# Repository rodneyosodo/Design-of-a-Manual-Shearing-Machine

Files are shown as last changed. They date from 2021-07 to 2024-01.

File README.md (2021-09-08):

# Design of a Manual Shearing Machine - Manufacturing-Technology-1-Project







## This project is done by:

1. Kelvin Gitu ENM221-0058/2017
2. Rodney David ENM221-0091/2017

## Manual Shearing Machine

Shearing is a method for cutting materials into small pieces using a shear knife using some force. Metal plates and sheets are cut using this method. The most predominant type of shearing machine is the hydraulic shearing machine. However, most small businesses are not able to acquire such machines and thus form our purpose. Our design is a simple manual shearing machine that can be readily made in a well-equipped workshop. It is also cheap to produce and can be done in a very short time. 
A computer-aided drawing of the machine is shown below.

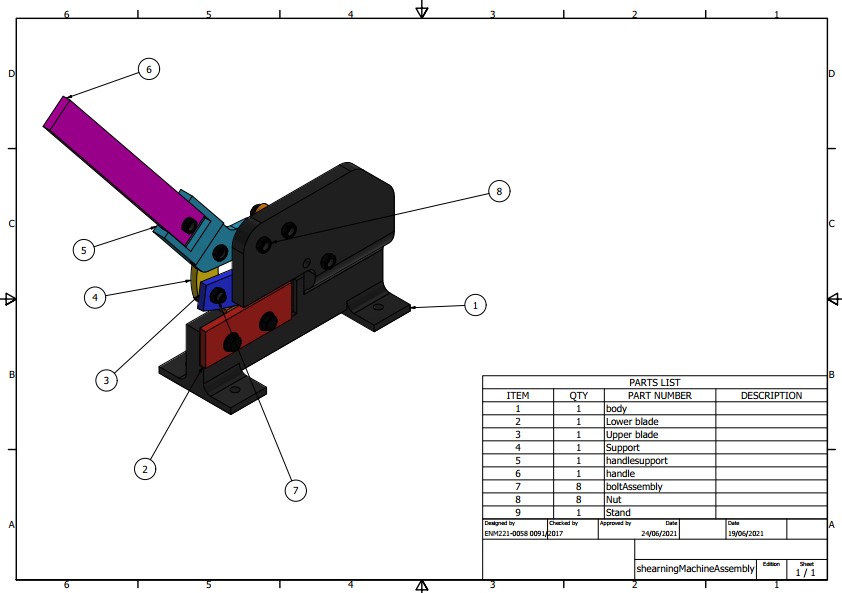
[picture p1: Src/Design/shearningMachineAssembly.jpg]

The assembly above consists of nine parts all of which can be produced in a workshop through processes such as turning, milling, shaping, drilling, among others. We also intend to use some of the parts from the shelves e.g bolt washer and nut. The handle might come as a rod or a tube with a rectangular cross-section from the manufacturer. This means it would have undergone some primary shaping. We would only need to surface finish it by grinding off unwanted material and painting.

## Manufacturing Processes

Primary shaping. As we had stated early some parts will come directly from the manufacturer. This includes the handle we can use a cylindrical handle or a cuboid handle. Probably it would have undergone a drawing operation.
Separation
1. Milling. This will be one of our core manufacturing processes. We can mill the remaining parts but we would prefer to use a CNC milling machine so as to achieve a high level of precision. We might use milling operations to the nut and bolt if they can not be found locally.
2. Lathe operations. The bolt washer and nut if they are not found locally we would start them off with lathe operations. These would include facing, turning, drilling, threading among others,
3. CNC Machining. Now, all the above operations can be completed in a programmable CNC machine. I guess this is our most important process. We wouldn’t discuss the advantages of CNC machining presents to use but we would rather explain some of the machining processes. We would use CNC milling to do most of our tasks. We would initially buy the billet material then place it on the milling table and program the machine to cut the specific geometry we want. Some of the parts we would mill include the Body, lower blade, upper blade, support, handle support and stand. 
4. Grinding. After machining the upper and lower blade we would grind it so as to ensure the knife edge is sharp enough. We aren’t sure if this can be done using the MasterCAM software but we are looking into it.
Joining
1. Welding. We intend to reinforce some of the bolted joints with welds specifically at the body. This is to ensure our body is rigid and has a longer life span. We aren’t sure if this can be done using the MasterCAM software but we are looking into it. We know it can be done using the Inventor CAM software.
2. Bolt and nut. This is the easiest and most convenient way to join some of our parts e.g the handle and also the blades to the body. This would provide a good joint ensuring the machining can last longer.
Coating
As our final process, we would like to paint the machine so as to increase its aesthetic appeal. We aren’t sure if this can be done using the MasterCAM software but we are looking into it.

## Presentation
Can be viewed from [here](https://prezi.com/view/DIa9HizP2NmdG6Iu90mM/)

## Project structure
```
.
├── Analysis
│   ├── 2021-07-30_22-48-34.mkv
│   ├── Images
│   │   ├── Autodesk_Logo_Black.png
│   │   ├── minus.png
│   │   ├── plus.png
│   │   └── shearningMachineAssembly.iam Stress Analysis Report 30_07_2021
│   │       └── 0
│   │           ├── Constraint_0_0.png
│   │           ├── Load_0_1.png
│   │           ├── Load_0_2.png
│   │           ├── Result_1_1.png
│   │           └── Result_1_8.png
│   ├── shearningMachineAssembly.iam Stress Analysis Report 30_07_2021.html
│   ├── Study Result.avi
│   └── Weld Bead Report.xls
├── Codes
│   ├── 1001.nc
│   ├── bodybottompart.mpf
│   ├── bodybottompart.NC
│   ├── upperblade.mpf
│   └── upperblade.NC
├── Design
│   ├── handle.dwg
│   ├── handle.ipt
│   ├── handle.pdf
│   ├── handlesupport.dwg
│   ├── handlesupport.ipt
│   ├── handlesupport.pdf
│   ├── lockfile.lck
│   ├── OldVersions
│   ├── README.md
│   ├── rendershearningMachineAssembly.png
│   ├── shearningMachineAssembly
│   │   ├── AIP
│   │   │   └── FEA
│   │   │       ├── dola00nj4.fins
│   │   │       └── Simulation.log
│   │   └── InCAD
│   │       └── FEA
│   │           ├── LICENSE.LOG
│   │           ├── pkfd50uhz.ECD
│   │           └── pkfd50uhz.OUT
│   ├── shearningMachineAssembly.dwg
│   ├── shearningMachineAssembly.iam
│   ├── shearningMachineAssembly.jpg
│   └── shearningMachineAssembly.pdf
├── MANUAL_SHEARING_MACHINE_PROJECT_REPORT.pdf
├── presentation.txt
└── README.md
```

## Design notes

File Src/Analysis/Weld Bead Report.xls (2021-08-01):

Document | ID | Type | Length | UoM | Mass | UoM | Area | UoM | Volume | UoM
C:\Users\Public\D\Desktop\Trash\Manufacturing-Technology-1-Project\Src\Design\bodyAssembly.iam
 | Fillet Weld 1 | Fillet | 110 | mm | 0.023 | kg | 5872.448 | mm^2 | 8443.037 | mm^3 | 110 mm | 0.023 kg | 5872.448 mm^2 | 8443.037 mm^3
 | Fillet Weld 2 | Fillet | 110 | mm | 0.023 | kg | 5872.448 | mm^2 | 8443.037 | mm^3 | 110 mm | 0.023 kg | 5872.448 mm^2 | 8443.037 mm^3
 | Fillet Weld 3 | Fillet | 50 | mm | 0.005 | kg | 1797.566 | mm^2 | 2026.715 | mm^3 | 50 mm | 0.005 kg | 1797.566 mm^2 | 2026.715 mm^3
 | Fillet Weld 4 | Fillet | 50 | mm | 0.005 | kg | 1797.566 | mm^2 | 2026.715 | mm^3 | 50 mm | 0.005 kg | 1797.566 mm^2 | 2026.715 mm^3
 | Fillet Weld 5 | Fillet | 50 | mm | 0.005 | kg | 1797.566 | mm^2 | 2026.715 | mm^3 | 50 mm | 0.005 kg | 1797.566 mm^2 | 2026.715 mm^3
 | Fillet Weld 6 | Fillet | 50 | mm | 0.005 | kg | 1797.566 | mm^2 | 2026.715 | mm^3 | 50 mm | 0.005 kg | 1797.566 mm^2 | 2026.715 mm^3
 |  |  | Length | Mass | Area | Volume
 | Fillet Weld 1 | Fillet | 110 mm | 0.023 kg | 5872.448 mm^2 | 8443.037 mm^3
 | Fillet Weld 2 | Fillet | 110 mm | 0.023 kg | 5872.448 mm^2 | 8443.037 mm^3
 | Fillet Weld 3 | Fillet | 50 mm | 0.005 kg | 1797.566 mm^2 | 2026.715 mm^3
 | Fillet Weld 4 | Fillet | 50 mm | 0.005 kg | 1797.566 mm^2 | 2026.715 mm^3
 | Fillet Weld 5 | Fillet | 50 mm | 0.005 kg | 1797.566 mm^2 | 2026.715 mm^3
 | Fillet Weld 6 | Fillet | 50 mm | 0.005 kg | 1797.566 mm^2 | 2026.715 mm^3

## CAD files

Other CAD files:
Src/Design/bodyAssembly.dwg
Src/Design/shearningMachineAssembly.dwg
Src/Design/Stand.dwg
Src/Design/handlesupport.dwg
Src/Design/handle.dwg
Src/Design/Upper blade.dwg
Src/Design/Support.dwg
Src/Design/Lower blade.dwg
Src/Design/body.dwg
Src/Design/OldVersions/shearningMachineAssembly.0003.dwg
Src/Design/OldVersions/bodyAssembly.0002.dwg
Src/Design/OldVersions/Stand.0002.dwg
Src/Design/OldVersions/Lower blade.0001.dwg
Src/Design/OldVersions/Support.0001.dwg
Src/Design/OldVersions/body.0001.dwg
Src/Design/Bolt.ipt
Src/Design/Lower blade.ipt
Src/Design/Nut.ipt
Src/Design/OldVersions/Bolt.0005.ipt
Src/Design/OldVersions/Lower blade.0005.ipt
Src/Design/OldVersions/Nut.0002.ipt
Src/Design/OldVersions/Stand.0004.ipt
Src/Design/OldVersions/Support.0004.ipt
Src/Design/OldVersions/Support.0005.ipt
Src/Design/OldVersions/Upper blade.0009.ipt
Src/Design/OldVersions/Washer.0004.ipt
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

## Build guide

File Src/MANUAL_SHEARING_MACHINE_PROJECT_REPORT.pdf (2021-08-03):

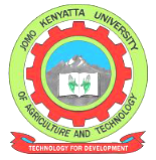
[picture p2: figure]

### JOMO KENYATTA UNIVERSITY OF AGRICULTURE AND TECHNOLOGY

### COLLEGE: COLLEGE OF ENGINEERING AND TECHNOLOGY

### SCHOOL: SCHOOL OF MATERIAL, MECHANICAL AND MANUFACTURING ENGINEERING

### DEPARTMENT: DEPARTMENT OF MECHATRONICS ENGINEERING

### UNIT CODE: EMT 2440

### UNIT TITLE: MANUFACTURING TECHNOLOGY

### YEAR OF STUDY: 4

TH

### ACADEMIC YEAR: 2021

### TASK: MANUAL SHEARING MACHINE PROJECT

NAME | REGISTRATION NO
KELVIN GITU | ENM221-0058/2017
RODNEY OSODO | ENM221-0091/2017

## Table of Contents

Abstract | 2
Introduction | 2
Problem Definition | 3
Design Requirements | 3
Design Description | 4
Design and Manufacturing Process | 5
Machining | 5
Body | 6
Lower blade | 8
Upper blade | 8
Stand | 9
Support | 10
Handle support | 11
Washer | 12
Joining | 12
Coating | 12
Evaluation | 13
Conclusion | 15
Challenges | 15
References | 16
Appendix | 17

## Abstract

This report presents the design of a manual shearing machine which is designed to increase the thickness of material it can cut in such a manner that the shearing force is great enough to cut material of width greater than 20mm. The objective of this project was to come up with a shearing machine that improves productivity by reducing labour costs (easy to use), meets client needs for small businesses by providing a design that can be fabricated in a workshop and increases worker safety. This is done by modifying the existing shearing machine by increasing blade angles and also increasing the structural rigidity of the shearing machine. The parts are modelled in Autodesk Inventor and machined using the Inventor CAM plugin. We made considerations in dimension and materials used so that the assembly could be manufactured locally at the machine shop.

## Introduction

A shearing machine is a machine that cuts a sheet of metal by reciprocating a linear motion with one blade moving relative to a fixed blade. Shearing is a general name for most sheet metal cutting, but in a specific sense, designates a cut in a straight line across a strip, sheet or bar. This procedure leaves a clean edge on the piece of the metal that is sheared or cut. Shearing machines are used to cut or shear metal sheets in many ways. The particular method chosen depends on several factors such as the size and shape of the parts required and the numbers needed. The moving cutting member of a shearing machine may be actuated by a hand lever in bench shearing machines, foot treadle in treadle guillotines or electric motor or hydraulic system in power guillotines.

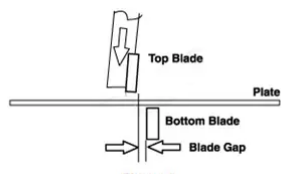
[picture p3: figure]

Figure 1: How shearing is done

## Problem Definition

During our attachment at the welding shop, we were able to encounter the manual shearing machine. Currently, it is able to cut up to a maximum of 20mm. This seems large but we saw an opportunity. We set out to increase the thickness the manual shearing machine could cut up to 30mm. Also, the shearing machines in the market include hydraulic swing beam shear, hydraulic guillotine shear, and electric shear. These off the shelf designs are very expensive and only top manufacturing plants can afford them. To make shearing available for small businesses, our design introduces a simple manual shearing machine that can be fabricated in a workshop at a relatively low cost. Our design is an adaptive redesign of an already existing solution, which has become outdated. The design is as shown below:

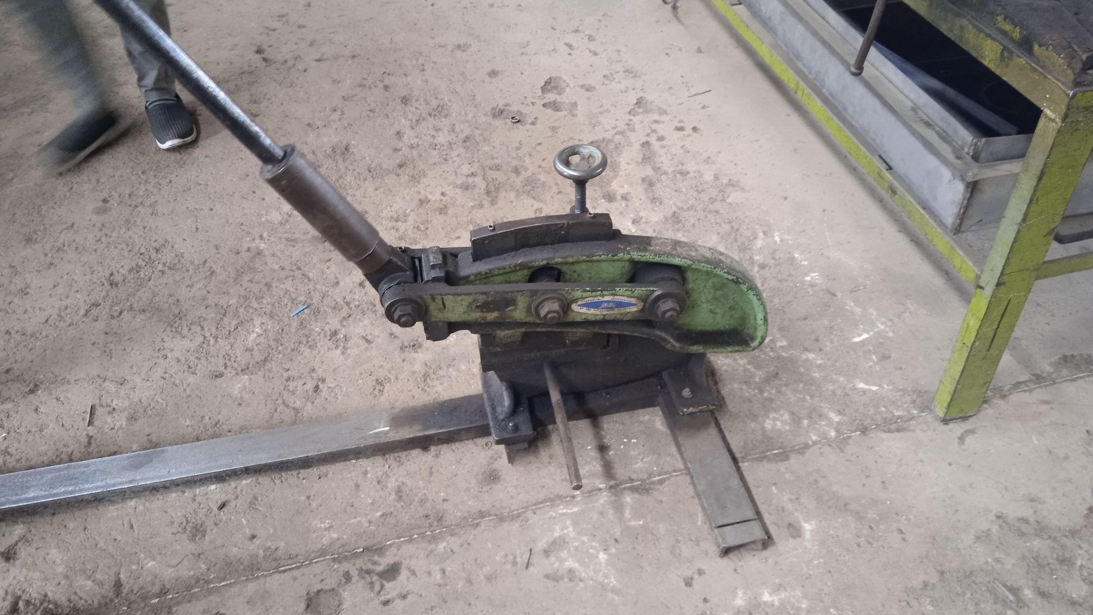
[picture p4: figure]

Figure 2: Manual Shearing Machine at Welding shop

## Design Requirements

The design shown in Figure 1 cuts sheet metal of up to 20mm. To improve on this design, we designed our manual shearing machine to shear sheets of up to 30mm.
The following formula is used to calculate the force required to shear sheet metal:

F = L • T • S
Where: F is the force required (Newtons), L is the length of the sheet to be cut (millimetres), T is the sheet thickness (millimetres) and S is the shear strength (N/mm ). ²

For a steel sheet metal with a thickness of 20mm, length is 20mm and shear strength of 300MPa, the force required to cut the shear metal will be:

F = L * T * S

F = 20 * 20 * 300

F = 120kN
Now, our design is supposed to do better, by generating enough force to cut up to 30mm thick of sheet metal.

F = 20 * 30 * 300

F = 180kN
This will be the requirement for our design. We also intend for our design to reduce labour costs, increase worker safety and increase the productivity of the process.

## Design Description

The design selected is constructed using only nine main parts from material that can be found readily: a combination of mild steel and stainless steel. The manual shearing machine has an upper and lower blade from which a sheet of metal can be cut. The upper blade is part of a lever system together with the handle through which shearing force is applied. The lower blade is fixed to the body part of the shearing machine which has a large surface area to absorb the pressure due to the shearing force and increase the stability of the machine. During a shearing operation, a sheet of metal is placed on the lower fixed blade, and a cutting force is applied through the handle. When the two blades make contact, the sheet metal is broken and separated according to the desired dimensions. The design is as shown in Figure 3.

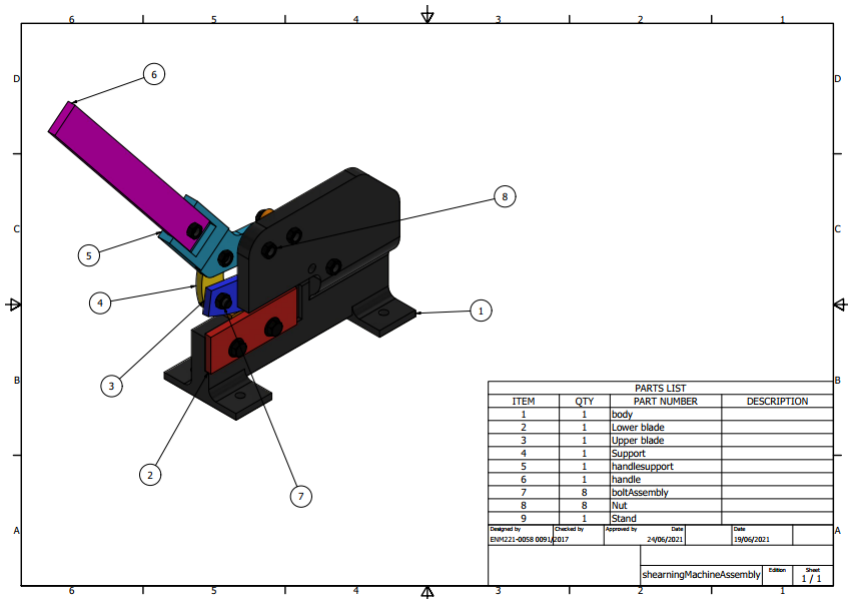
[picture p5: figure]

Figure 3. CAD Drawing of the Manual Shearing Machine

## Design and Manufacturing Process

The manual shearing machine design is an assembly of various parts and to describe its production process, we need to discuss the manufacture of the individual parts. In coming up with the parts, various workshop processes are applied, including turning, milling, drilling, among others. Some parts such as the fasteners (nuts and bolts), the washer and the handle were bought off the shelf. The other parts were first developed using CAD software, and we used Autodesk Inventor.
Manufacturing processes applied include:

### 1. Machining

CNC Machining. This is the most important machining process as most of our parts will be produced in a CNC machine. We will initially buy the billet material then place it on the milling table and program the machine to cut the specific geometry we want. Some of the parts we mill include the body, lower blade, upper blade, support, handle support and stand. The CNC milling process has four distinct stages:
- CAD model design.
- CAD model design conversion to a CNC program
- CNC milling machine setup
- Milling operation execution
Now let us take a look at the various parts, their CAD model designs, and their CNC programs to be executed in a milling machine. A computer-aided manufacturing software will be used to generate the CNC program. We decided to use the Siemens 840D due to its similarity with the CNC machine at the machine shop. This will actually help us do the physical analysis of our design if we were to be given a go-ahead to machine one of the parts.
a. Body

To produce the body in Figure 4, we decided to use a modular approach since machining the whole body altogether is a difficult operation. We broke the body into 3 main pieces, the bottom part, the top part and the standoffs. These individual parts are now able to be machined using a milling operation. We set up an initial stock which is an extra 5 mm at the top and an extra 2mm on the sides. The first operation was facing the required height of the workpiece. This was done with even multiple depths of 2mm spacing. Then we followed up by adaptive milling which is a 3D milling technique. We finally finished up with drilling the holes onto the workpiece. This operation was the same for all the parts of the body. We used flooding when applying coolant since our tool could not be able to deliver coolant inside. We thought of using air suction by keeping in mind the CNC at the machine shop, so we decided flooding was the better approach. We then used two joining techniques; welding and the use of nuts and bolts. We joined the standoffs to the bottom part with welding after having placed the bottom part in a slot on the standoffs. Joining the top part and bottom part was done mainly using the nuts and bolts. We finally reinforced it using welding with a fillet shape. The weld bead report is in Table 1.

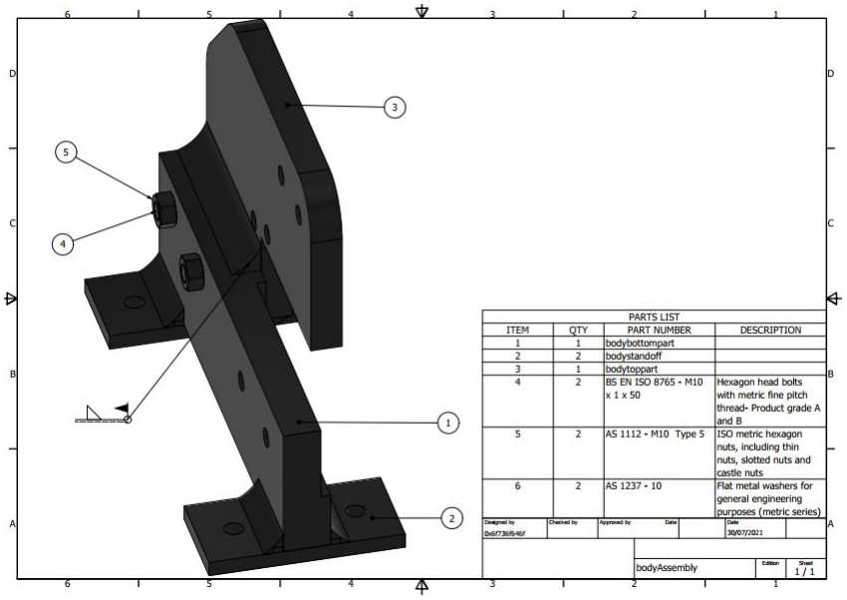
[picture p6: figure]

Figure 4. CAD Model of the Body

| | Length | Mass | Area | Volume
Fillet Weld 1 | Fillet | 110 mm | 0.023 kg | 5872.448 mm 2 | 3 8443.037 mm
Fillet Weld 2 | Fillet | 110 mm | 0.023 kg | 5872.448 mm 2 | 3 8443.037 mm
Fillet Weld 3 | Fillet | 50 mm | 0.005 kg | 1797.566 mm 2 | 3 2026.715 mm
Fillet Weld 4 | Fillet | 50 mm | 0.005 kg | 1797.566 mm 2 | 3 2026.715 mm
Fillet Weld 5 | Fillet | 50 mm | 0.005 kg | 1797.566 mm 2 | 3 2026.715 mm
Fillet Weld 6 | Fillet | 50 mm | 0.005 kg | 1797.566 mm 2 | 3 2026.715 mm

Table 1: Weld bead report

b. Lower blade

To come up with the lower blade the first manufacturing operation was facing, using a face mill of diameter 50mm. This operation reduced the workpiece to the required height. One edge was turned at an angle as it would form the cutting edge of the blade. Since we have a sloping cutting edge we decided to place it in a Z-direction such that the slant was an incremental downwards slope. We used additive machining, a form of 3D machining, to be able to obtain the contours on the blade. Once the dimensions of the part were achieved, the two 10 mm diameter holes were created using a drill using the rapid out technique.

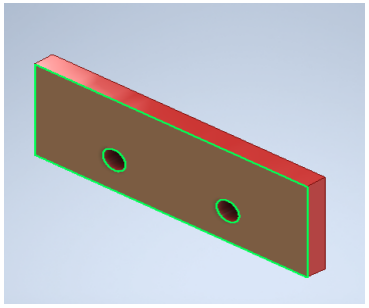
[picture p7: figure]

Figure 5. CAD Model of the Lower Blade

c. Upper blade

Face milling, end milling, and drilling are the operations carried out to come up with this part. We first reduced the workpiece to the required height using a face mill, which was followed by adaptive milling to establish the shape of the blade. In this operation, the milling tool axially follows the path with a predefined geometry. The two holes that would form the assembly were drilled into place.

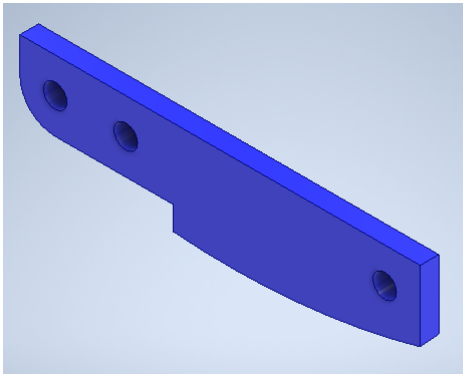
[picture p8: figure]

Figure 6. CAD Model of Upper Blade

d. Stand

Due to its design complexity, we decided to do a modular approach too. Here we split the stand into three different parts. The circular part was turning on a CNC lathe while the supporting beam together with the base was milled. For the circular part, we bought stock then we faced it off. This was done by a right-hand turning tool. We set the centre point at an offset of 1 mm from the true centre in order to get all of the material out during facing. We did multiple passes with 3 passes 2 mm apart. We continued to the turning where we defined it as profile roughing. We turned up to the end of the workpiece. We did multiple passes 1 mm apart. We then drilled the inside hole using the rapid out technique up to the end and finally parted off the workpiece from the stock using a grooving tool.

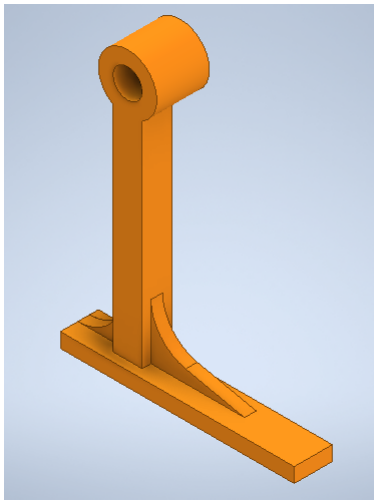
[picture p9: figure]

Figure 7. CAD Model of the Stand

e. Support

We first reduced the height of the workpiece using a facing operation. The two holes were drilled into place. We then machined the part using adaptive milling which maintains a consistent tool path and chip load which results in faster, smoother cutting.

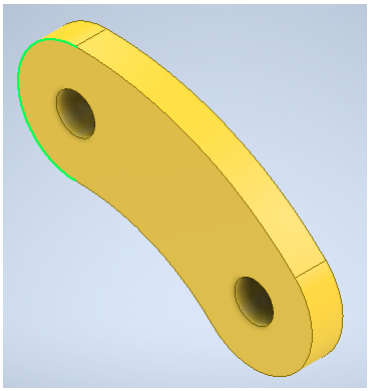
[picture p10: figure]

Figure 8. CAD Model of the Support

f. Handle support

We initially intended to use plasma cutting but the plasma cutting at the welding workshop isn’t CNC operated. We then decided to use the milling operation. Two facing operations were conducted to come up with the two heights on the other side of the top of the workpiece. On one end of the workpiece, we created a flat bottomed cavity using another end milling operation. Joining holes were drilled into the workpiece, after which the final operation, adaptive milling, was executed.

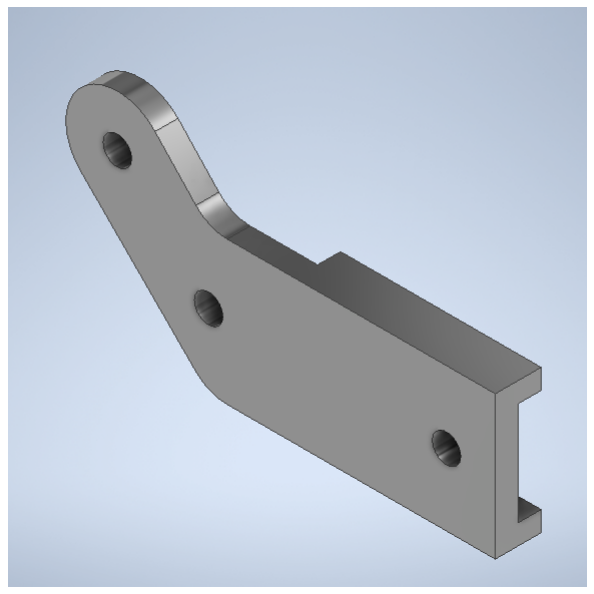
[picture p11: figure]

Figure 9. CAD Model of the Handle Support

g. Washer

This was purchased at the local stores together with the nuts and bolts used for assembly

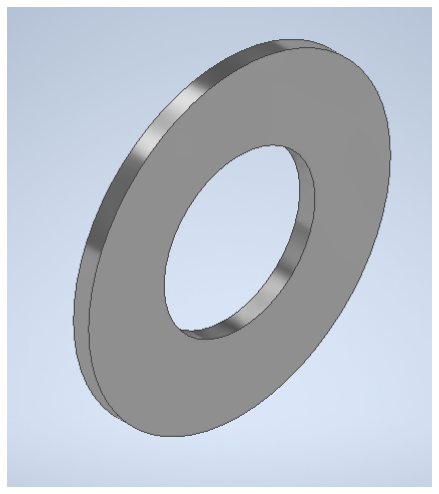
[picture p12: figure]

Figure 10. CAD Model of the Washer

### 2. Joining

After coming up with the individual parts, we need to put multiple parts together to make one piece. Some of the joining processes used include welding and the use of fasteners (nuts and bolts). The body is fabricated as three parts and joined together using a weld. Arc welding is the most preferred method.

The other parts are assembled together using the fasteners. The lower blade is attached to the body using bolts and nuts. The support, handle, handle support and upper blade are all joined together using bolts and nuts.

### 3. Coating

The final manufacturing process is coating both for aesthetic value and to protect against surface corrosion, that is, rusting.

## Evaluation

After coming up with the design, and manufacturing of the shearing machine, we need to make sure it works by simulating it in the CAD software.
This was done through dynamic simulation and Finite element analysis. For Dynamic simulation, we introduced a torque of 300.000 N/mm on the pivot of the lower blade to be able to see if the handle could be driven down to simulate the pressing action. This was justified as the handle moved down simulating the cutting mechanism. We also checked our mechanism and found out that 4 bodies were mobile with a 1 degree of freedom.
For the Finite Element Analysis, we were testing the maximum load the shearing machine can hold before fracture. We placed a test material on the bed which produces an opposite force of magnitude 10N majorly on the z-axis. We then added a 100N push force on the handle and observed the changes. The body was selected to be fixed while the blade had a frictionless surface to allow smooth motion.
Name | Steel, Mild
General | Mass Density | 7.85 g/cm^3
| Yield Strength | 207 MPa
| Ultimate Tensile Strength | 345 MPa
Stress | Young's Modulus | 220 GPa
| Poisson's Ratio | 0.275 ul
| Shear Modulus | 86.2745 GPa
Part Name(s) | Body.ipt, Lower blade.ipt, Upper blade.ipt, Support.ipt, handlesupport.ipt, handle.ipt, Stand.ipt

Name | Stainless Steel
General | Mass Density | 8 g/cm^3
| Yield Strength | 250 MPa
| Ultimate Tensile Strength | 540 MPa
Stress | Young's Modulus | 193 GPa
| Poisson's Ratio | 0.3 ul
| Shear Modulus | 74.2308 GPa
Part Name(s) | Bolt.ipt, Washer.ipt, Nut.ipt, Bolt.ipt

Table 2: Initial conditions

From our results, we were able to see that this motion induced a reaction moment of 1.12543 Nm.

Name | Minimum | Maximum
Volume | 1112060 mm^3
Mass | 8.73379 kg
Von Mises Stress | 0.000000946634 MPa | 5.50151 MPa
1st Principal Stress | -0.770633 MPa | 2.74524 MPa
3rd Principal Stress | -5.69371 MPa | 0.262106 MPa
Displacement | 0 mm | 0.00527388 mm
Safety Factor | 15 ul | 15 ul
Table 3: Finite Element Analysis

With a 15ul safety factor, we are at liberty to say that this machine increases its lifetime by a great margin. The maximum stress occurs at the cutting region demonstrated by Figure 10 below.

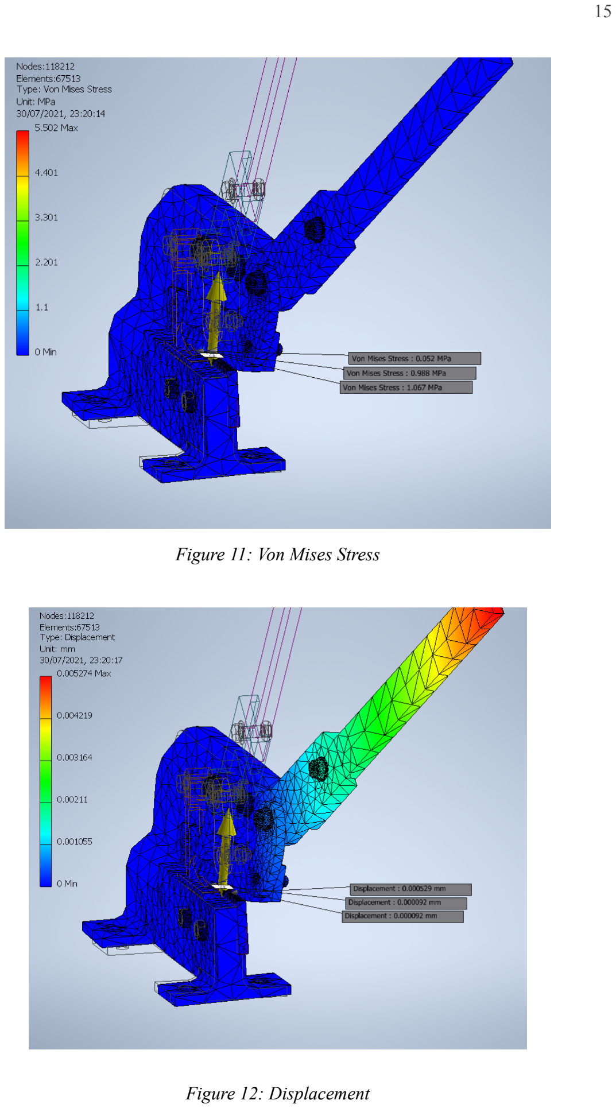
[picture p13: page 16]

Figure 11: Von Mises Stress

Figure 12: Displacement

As demonstrated we can be able to see that the handle is the one that moves, objecting to the physics behind the shearing machine.

## Conclusion

The design above seeks to employ a cheap and reliable way to cut sheets of metal. As the design procedure shows, it can be produced readily and quickly using basic workshop processes, including facing, turning, drilling among others. We have also proved that it has increased functionality compared to the previous design. As per our design requirements, our design increases the cutting force, thus enabling thicker sheets to be cut. Our design is also quite reliable as evidenced by the 15ul safety factor.

## Challenges

1. A complex design that needs casting processes.
2. Obtaining MasterCAM as it failed to start even with the Home education license.

## References

1. Merril L. Ridgeway, Kenneth E. Olding "MechanicalPress, Especially A Cupping Press", United StatesPatent, 3902347, (1975) Page 23 -30.
2. E. Paul. Degarmo, “Shearing in Metal Cutting”, Pages 518-528, Materials and Processes in Manufacturing, Eighth Edition, 2003, Prentice Hall of India Pvt Ltd.
3. Emil Gustafsson, “Experiments on sheet metal shearing”, Division of Mechanics of Solid Materials Department of Engineering Sciences and Mathematics Luleå University of Technology, SE-971 87 Luleå, Sweden
4. Z. Klim, E. Ennajimi, M. Balazinski and C. Fortin, Cutting Tool Reliability Analysis for Variable Feed Milling Of 17-4ph Stainless Steel.
5. Qehaja, N.; Bunjaku, A.; Salihu A. &Zeqiri, H., The Reliability of The Metal Cutting Tools on The Bases Of The Technological Criteria of Consumption Method
6. R. Hambli, A. Potiron, and A. Kobi, “Application Of Design Of Experiment Technique For Metal Blanking Processes Optimization,” Mécanique& Industries, vol. 4, no. 3, pp. 175
7. Joseph E. Shigley, Mechanical Engineering Design, Sixth Edition, Tata Mcgraw Hill, 2005.
8. Bhandari V.B., Design Of Machine Elements, eighteenth edition, Mcgraw Hill Companies, 2003.

## Appendix

1. https://github.com/KelvinGitu/Manufacturing-Technology-1-Project Project link
2. https://github.com/KelvinGitu/Manufacturing-Technology-1-Project/tree/main/Src/Co des (https://github.com/KelvinGitu/Manufacturing-Technology-1-Project/tree/main/Src/Codes) Machining codes
3. Example of milling part

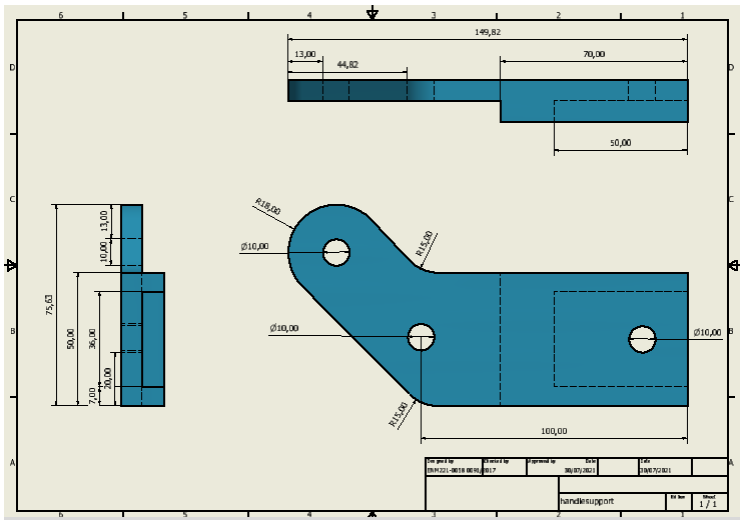
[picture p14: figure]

Figure 12: Handle support
4. Sample Generated codes for the handle support

; %_N_HANDLESUPPORT_MPF
N10 ; handlesupport
N11 ; T1 D=50 CR=0 - ZMIN=16 - face mill
N12 ; T2 D=5 CR=0 - ZMIN=0.51 - flat end mill
N13 ; T30 D=10 CR=0 TAPER=118deg - ZMIN=0 - drill
N14 WORKPIECE(,,,"BOX",112,21,0,80,74.91,37.815,-74.91,-37.815) N15 G90 G94
N16 G71
N17 G64
N18 G17
N19 G0 SUPA Z0 D0

N20 ; Face1
N21 T1 D1
N22 M6
N23 T2
N24 S955 M3
N25 G54
N26 G0 X107.41 Y-24.375
N27 G0 Z36
N28 M8
N29 G0 Z26

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
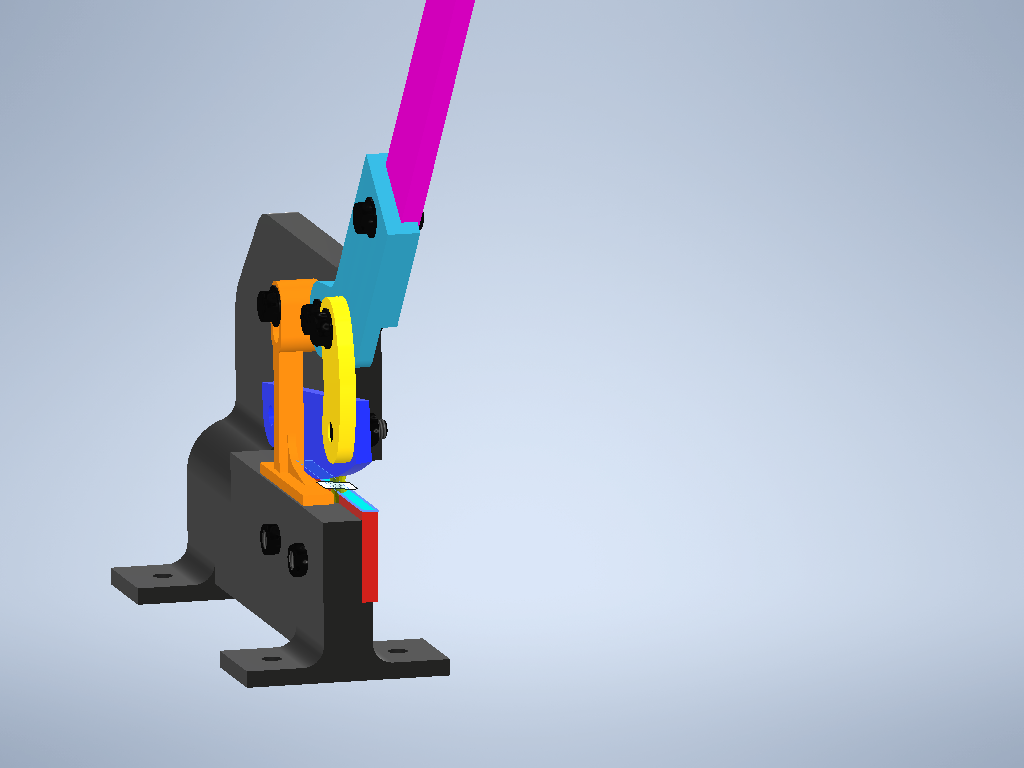
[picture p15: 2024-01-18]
Src/Analysis/Images/shearningMachineAssembly.iam Stress Analysis Report 30_07_2021/0/Load_0_1.png

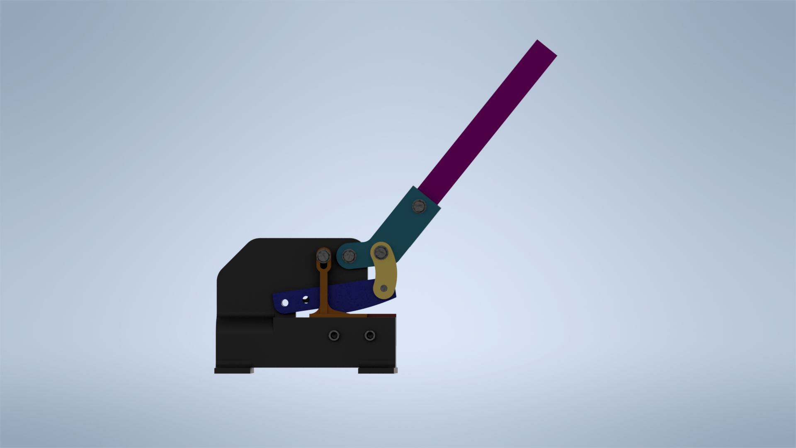
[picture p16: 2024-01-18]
Src/Design/rendershearningMachineAssembly.png

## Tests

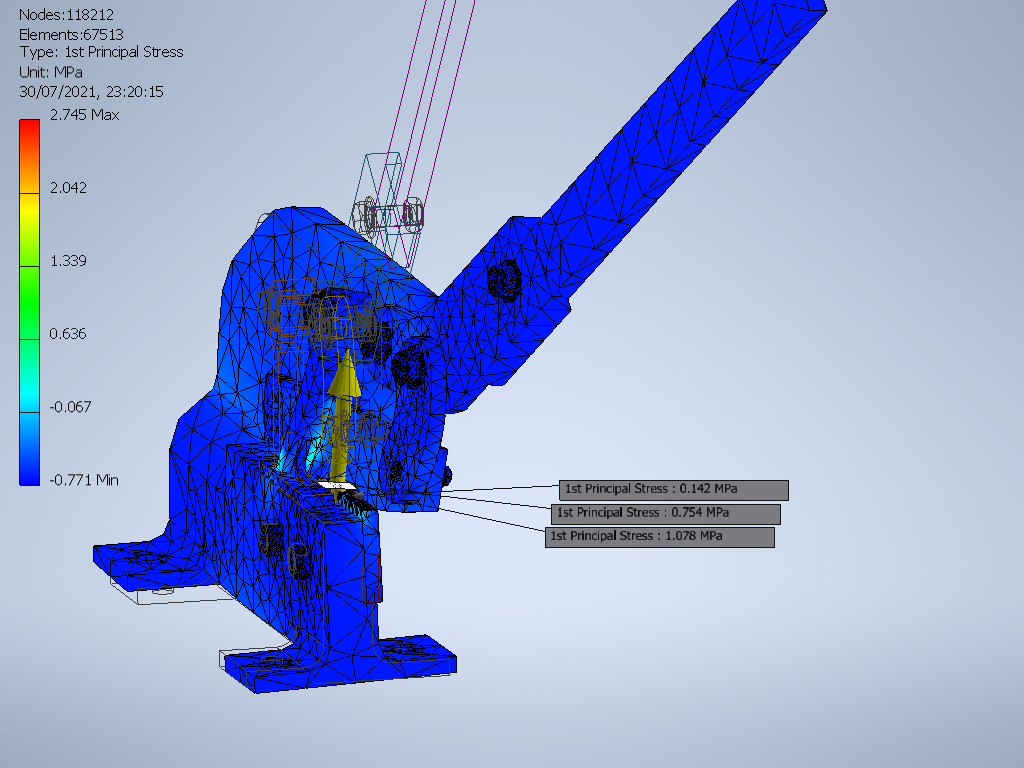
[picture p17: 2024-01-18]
Src/Analysis/Images/shearningMachineAssembly.iam Stress Analysis Report 30_07_2021/0/Result_1_6.png

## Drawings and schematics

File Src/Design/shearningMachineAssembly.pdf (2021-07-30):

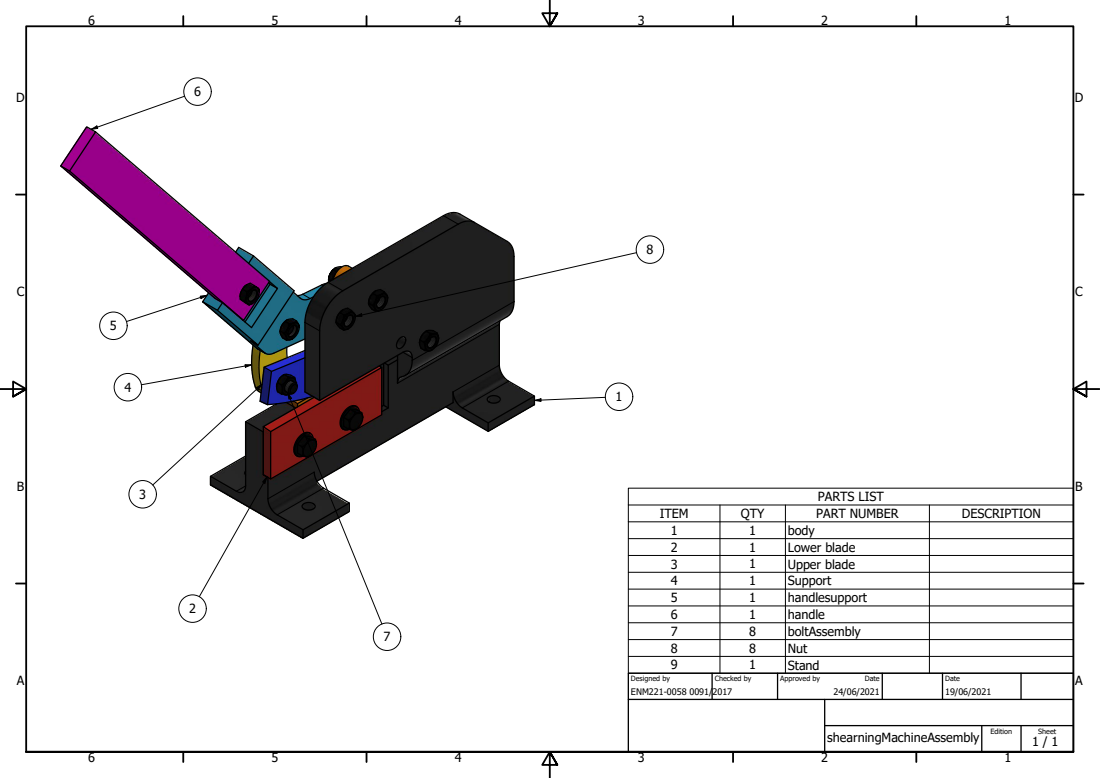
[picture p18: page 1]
PARTS LIST

ITEM | QTY | PART NUMBER | DESCRIPTION
1 | 1 | body
2 | 1 | Lower blade
3 | 1 | Upper blade
4 | 1 | Support
5 | 1 | handlesupport
6 | 1 | handle
7 | 8 | boltAssembly
8 | 8 | Nut
9 | 1 | Stand

Designed by ENM221-0058 0091/2017 | Checked by | Approved by Date 24/06/2021 | | Date 19/06/2021

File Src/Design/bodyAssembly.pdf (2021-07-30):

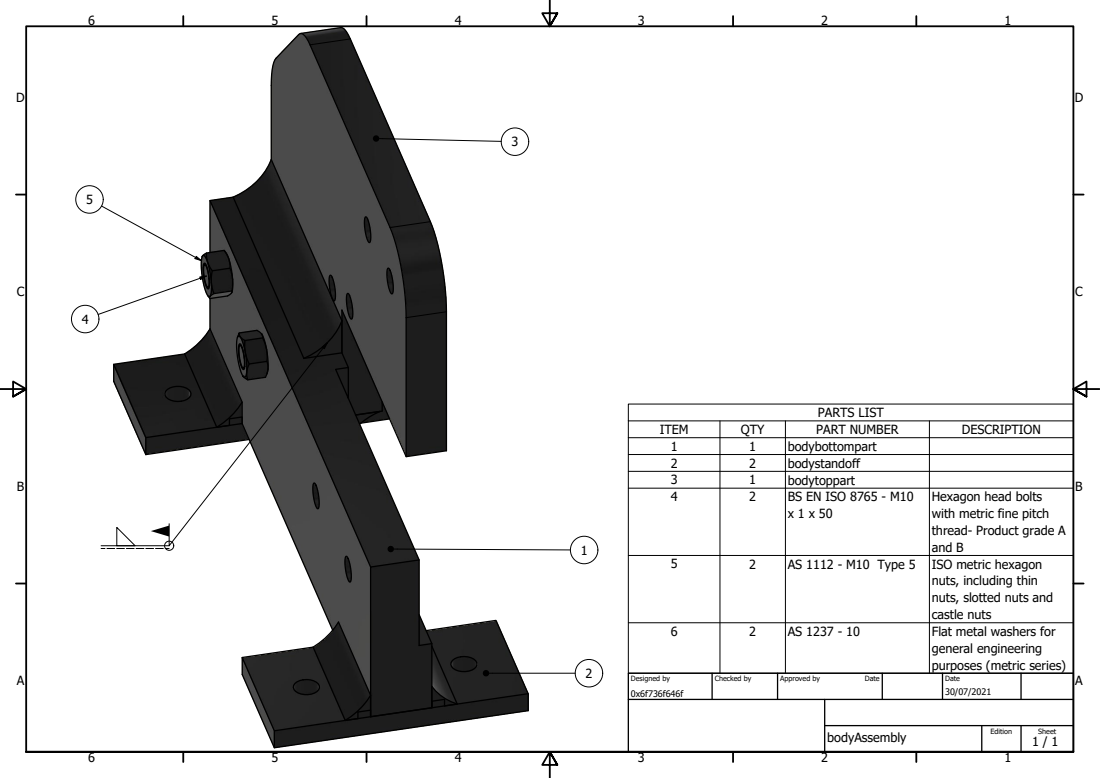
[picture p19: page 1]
PARTS LIST

ITEM | QTY | PART NUMBER | DESCRIPTION
1 | 1 | bodybottompart
2 | 2 | bodystandoff
3 | 1 | bodytoppart
4 | 2 | BS EN ISO 8765 - M10 x 1 x 50 | Hexagon head bolts with metric fine pitch thread- Product grade A and B

5 | 2 | AS 1112 - M10 Type 5 | ISO metric hexagon nuts, including thin nuts, slotted nuts and castle nuts

6 | 2 | AS 1237 - 10 | Flat metal washers for general engineering purposes (metric series)

Designed by 0x6f736f646f | Checked by | Approved by | | Date 30/07/2021

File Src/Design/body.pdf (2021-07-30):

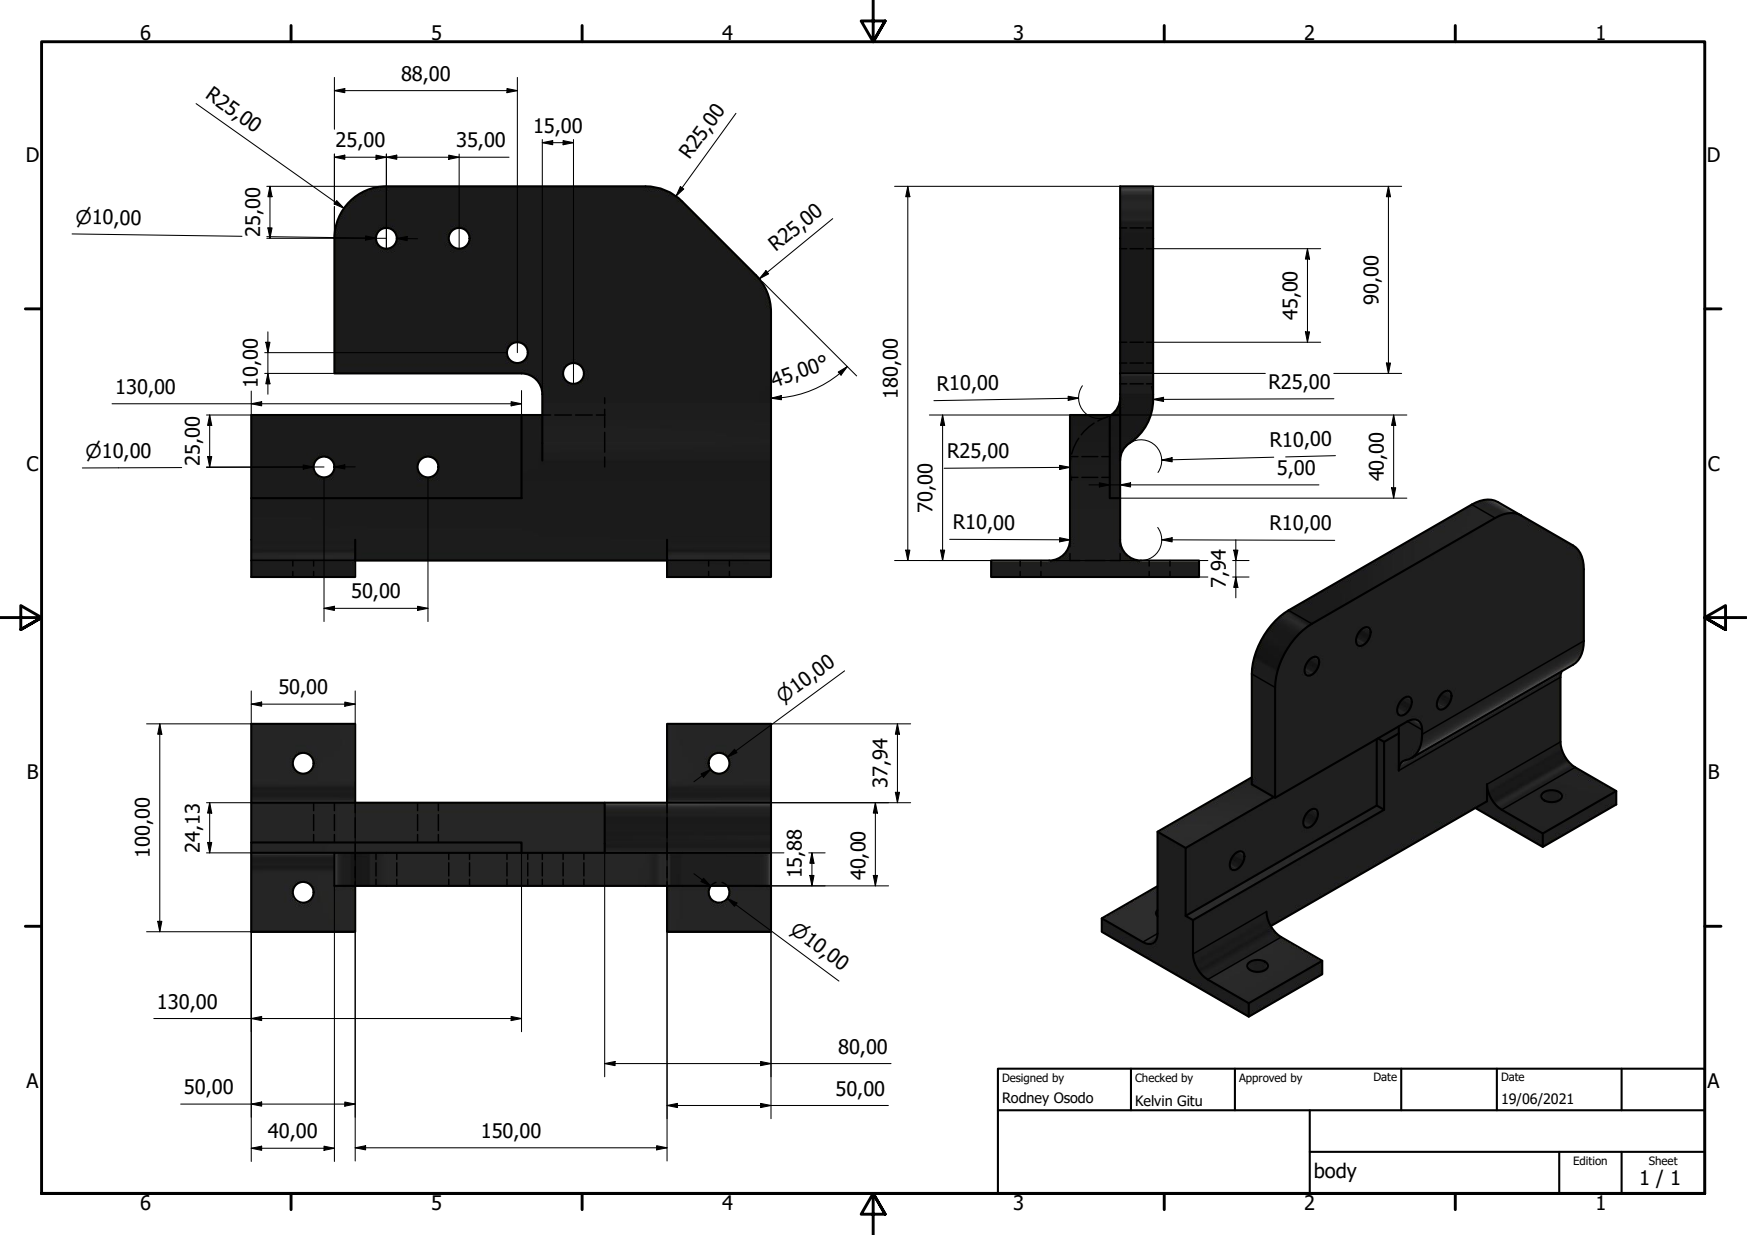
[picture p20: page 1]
Rodney Osodo; Kelvin Gitu; Designed by; Checked by; Approved by; Date

body | Edition | Sheet 1 / 1

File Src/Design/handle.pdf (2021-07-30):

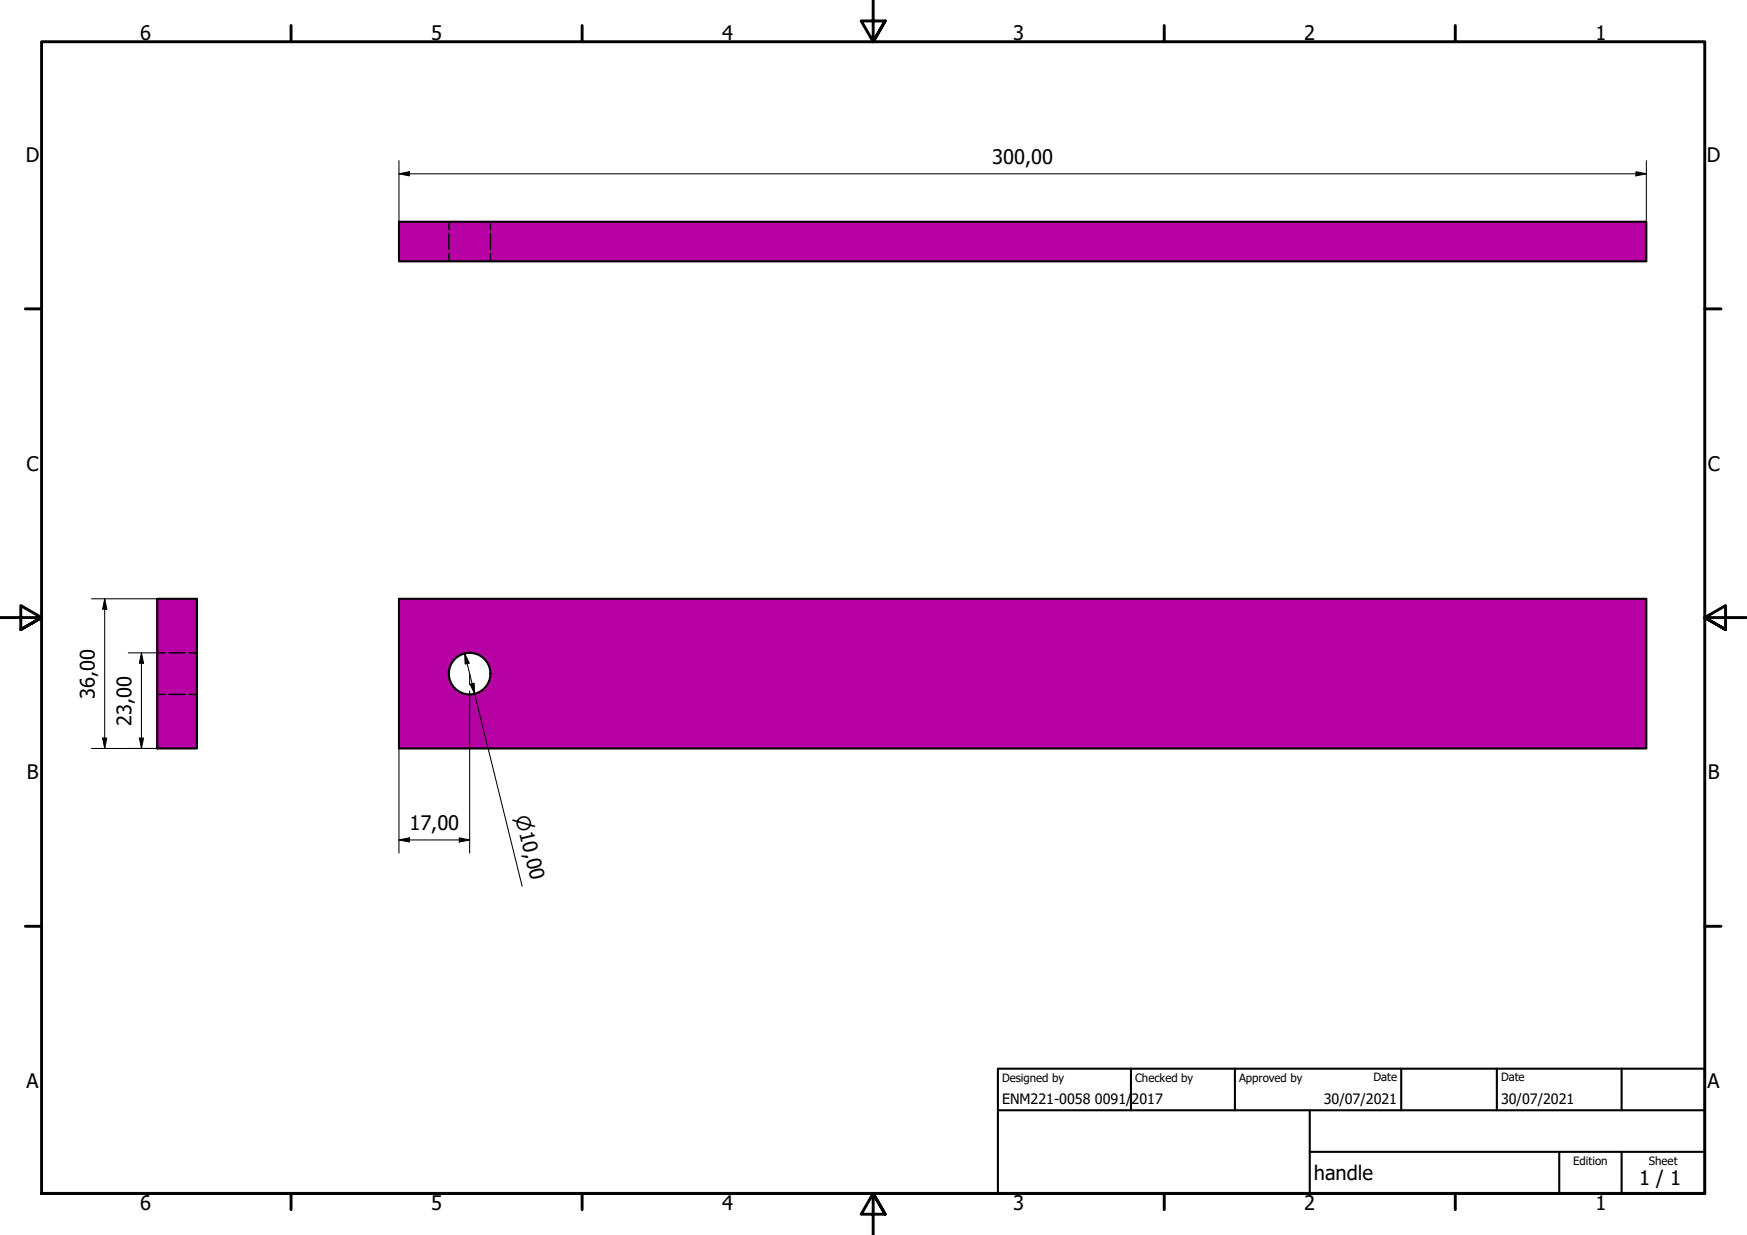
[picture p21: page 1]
ENM221-0058 0091/2017; Designed by; Checked by; Approved by; Date

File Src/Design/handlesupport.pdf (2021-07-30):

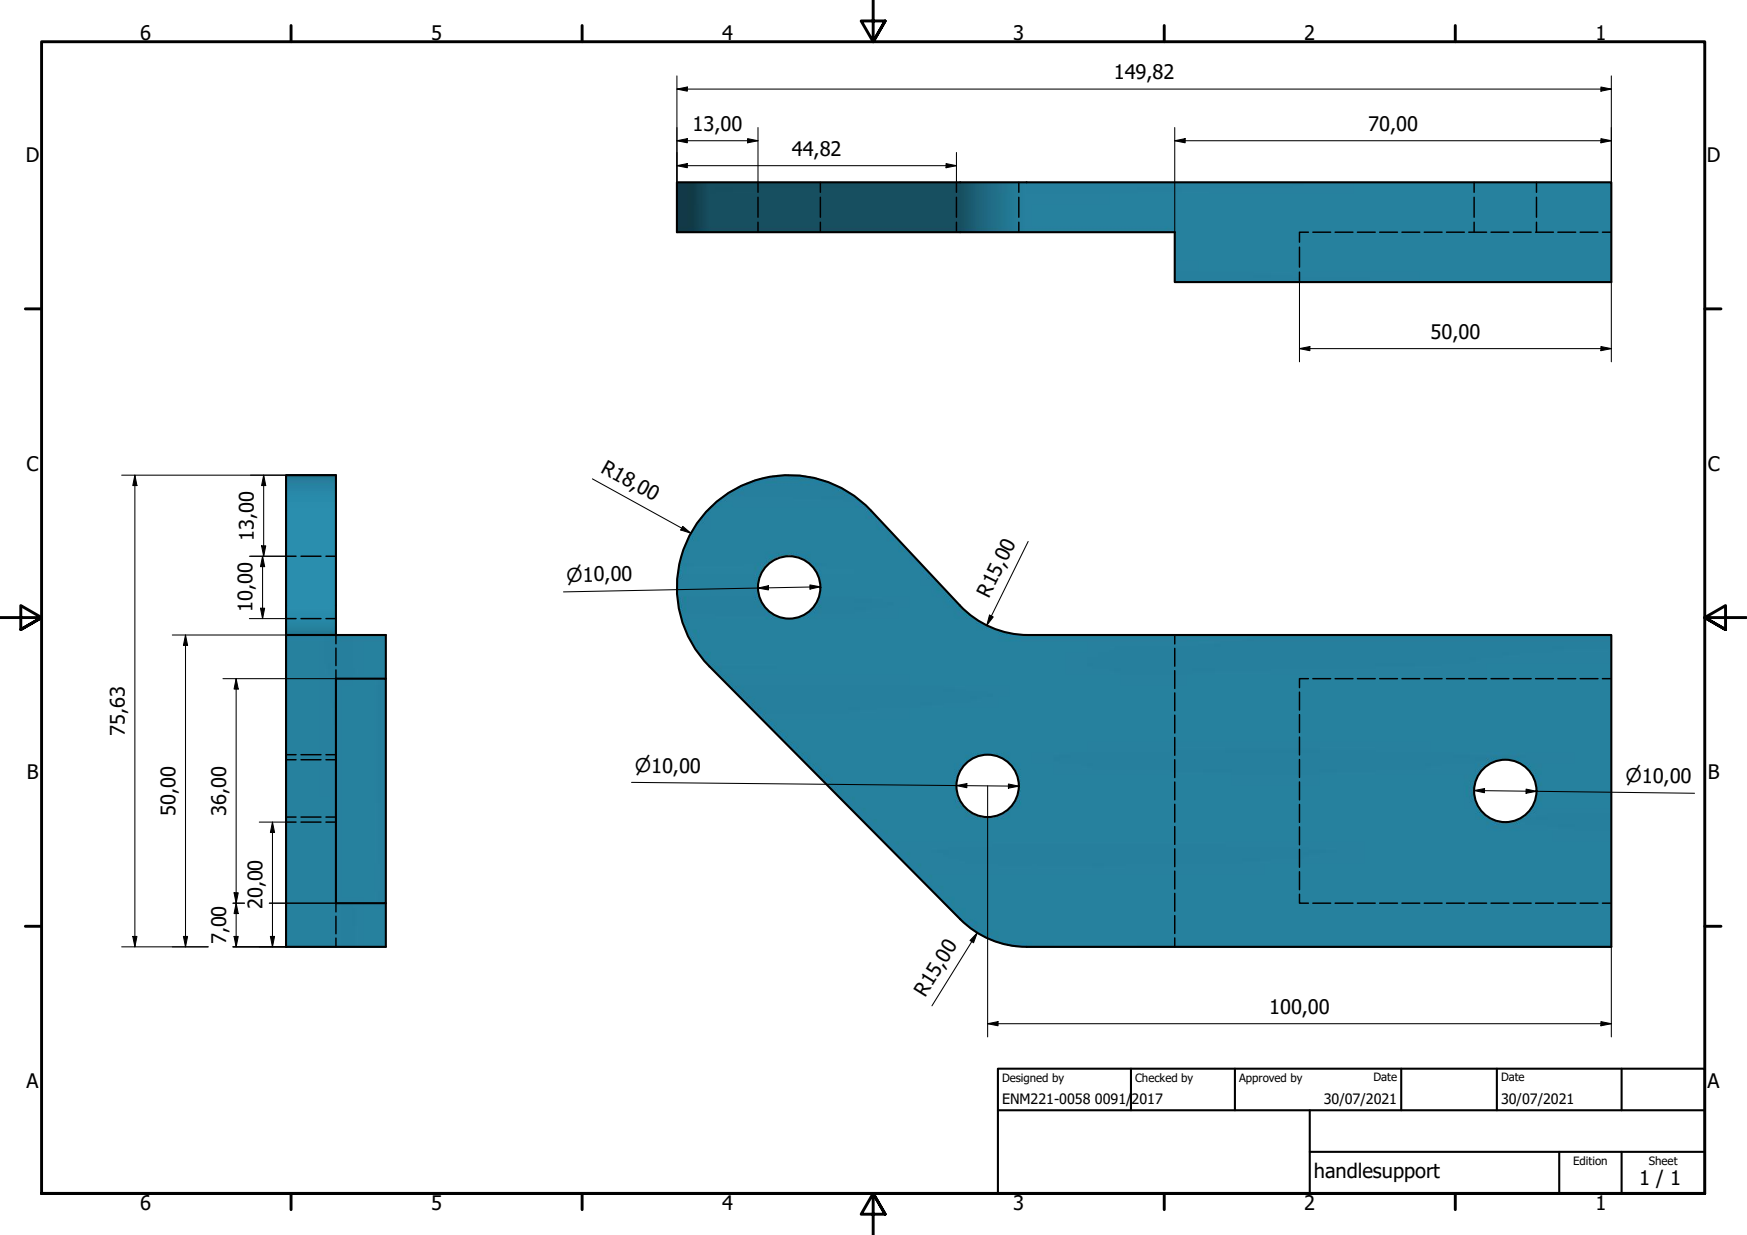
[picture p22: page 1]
ENM221-0058 0091/2017; Designed by; Checked by; Approved by; Date

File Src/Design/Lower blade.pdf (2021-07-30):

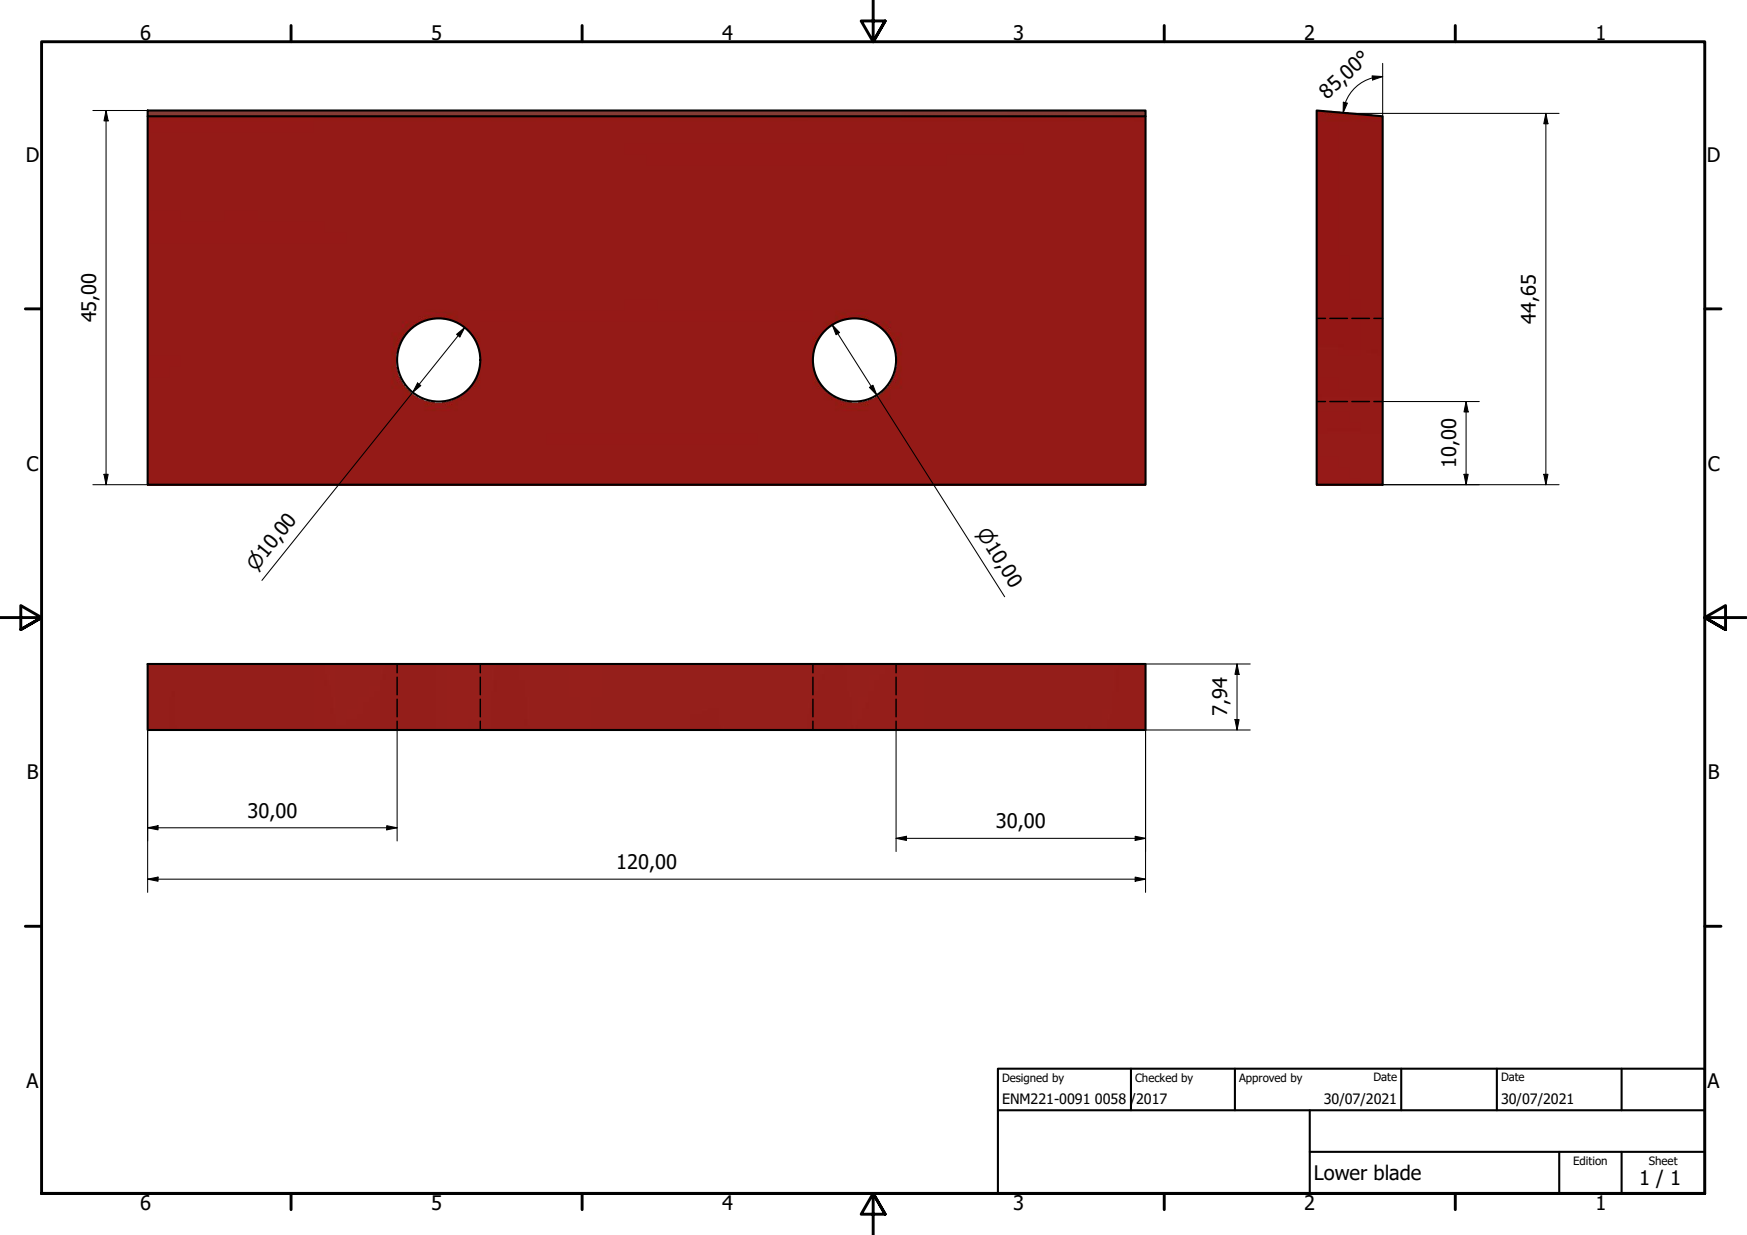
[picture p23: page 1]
Lower blade; ENM221-0091 0058; Designed by; Checked by; Approved by; Date

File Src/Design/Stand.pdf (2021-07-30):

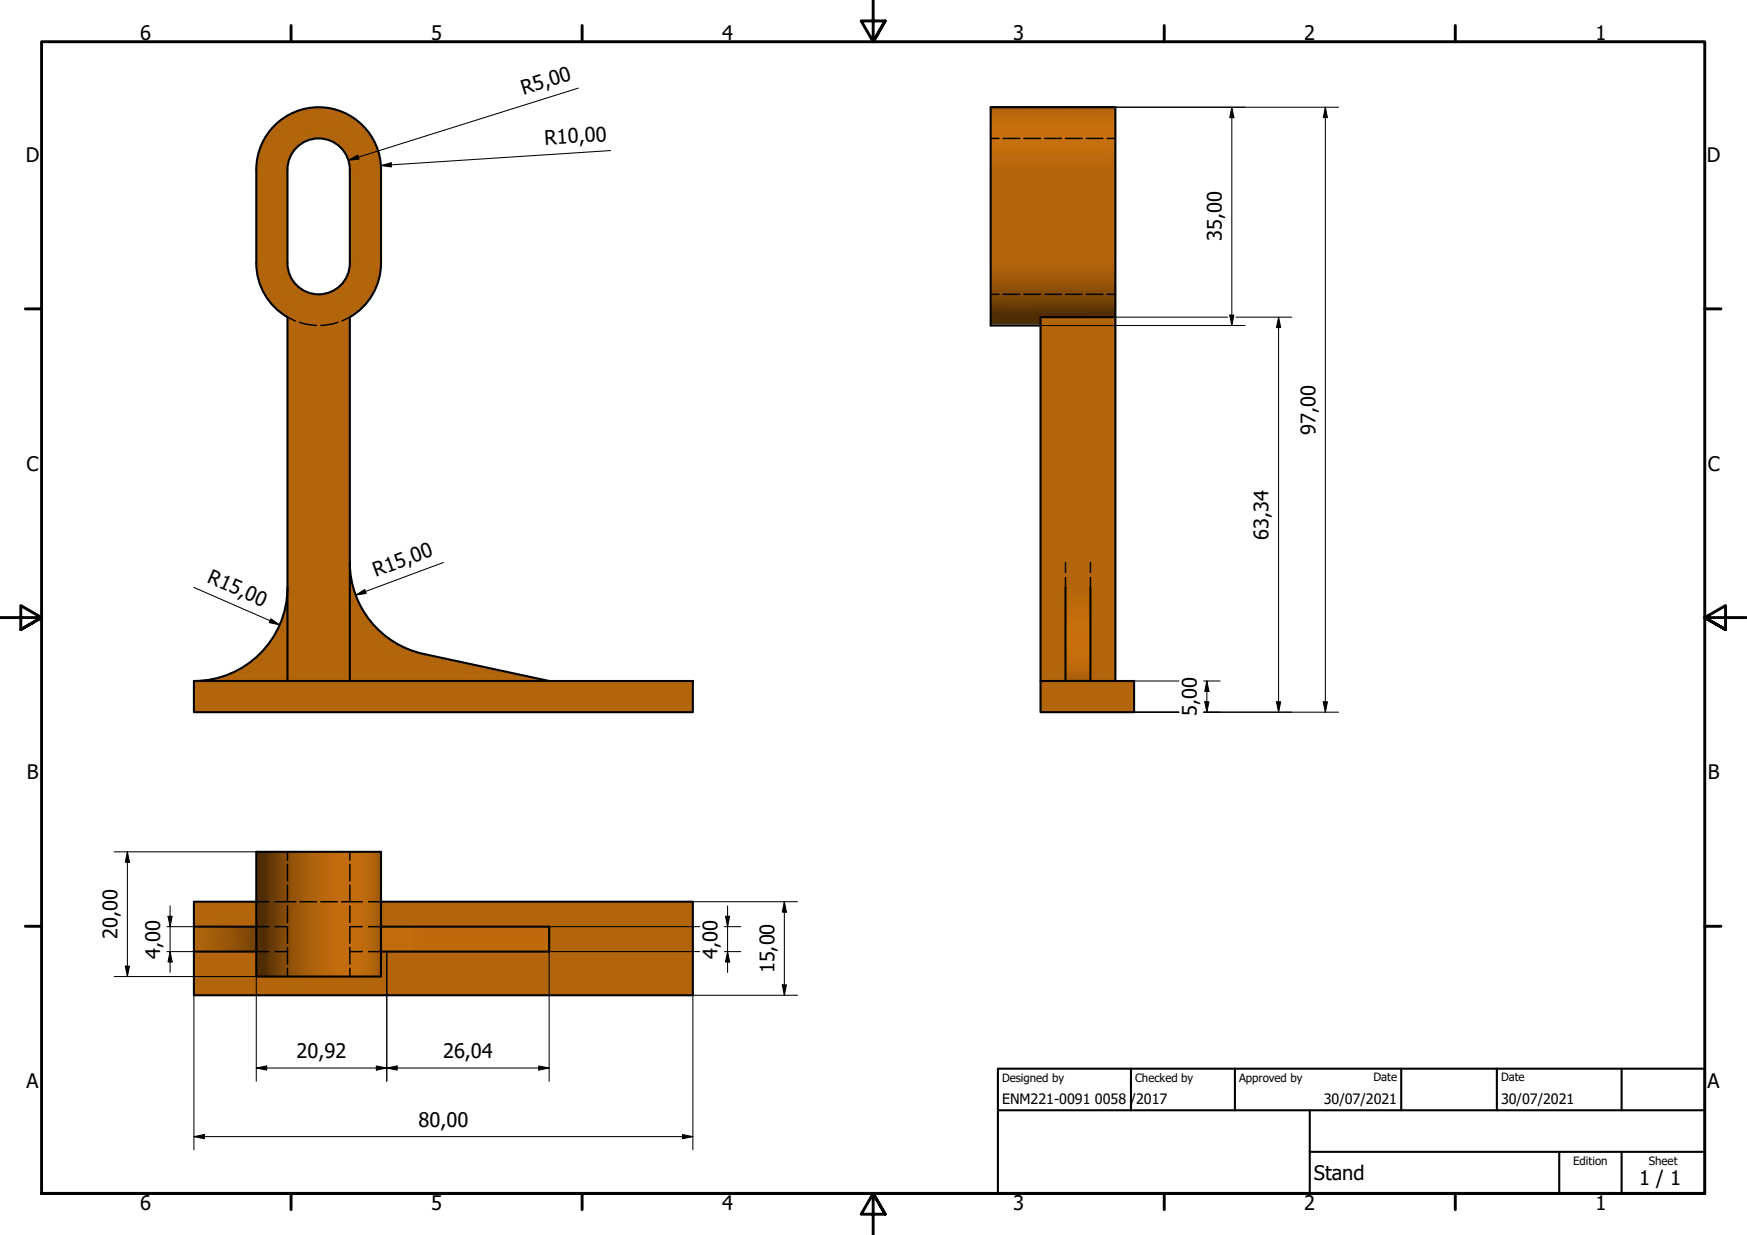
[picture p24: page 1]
ENM221-0091 0058; Designed by; Checked by; Approved by; Date

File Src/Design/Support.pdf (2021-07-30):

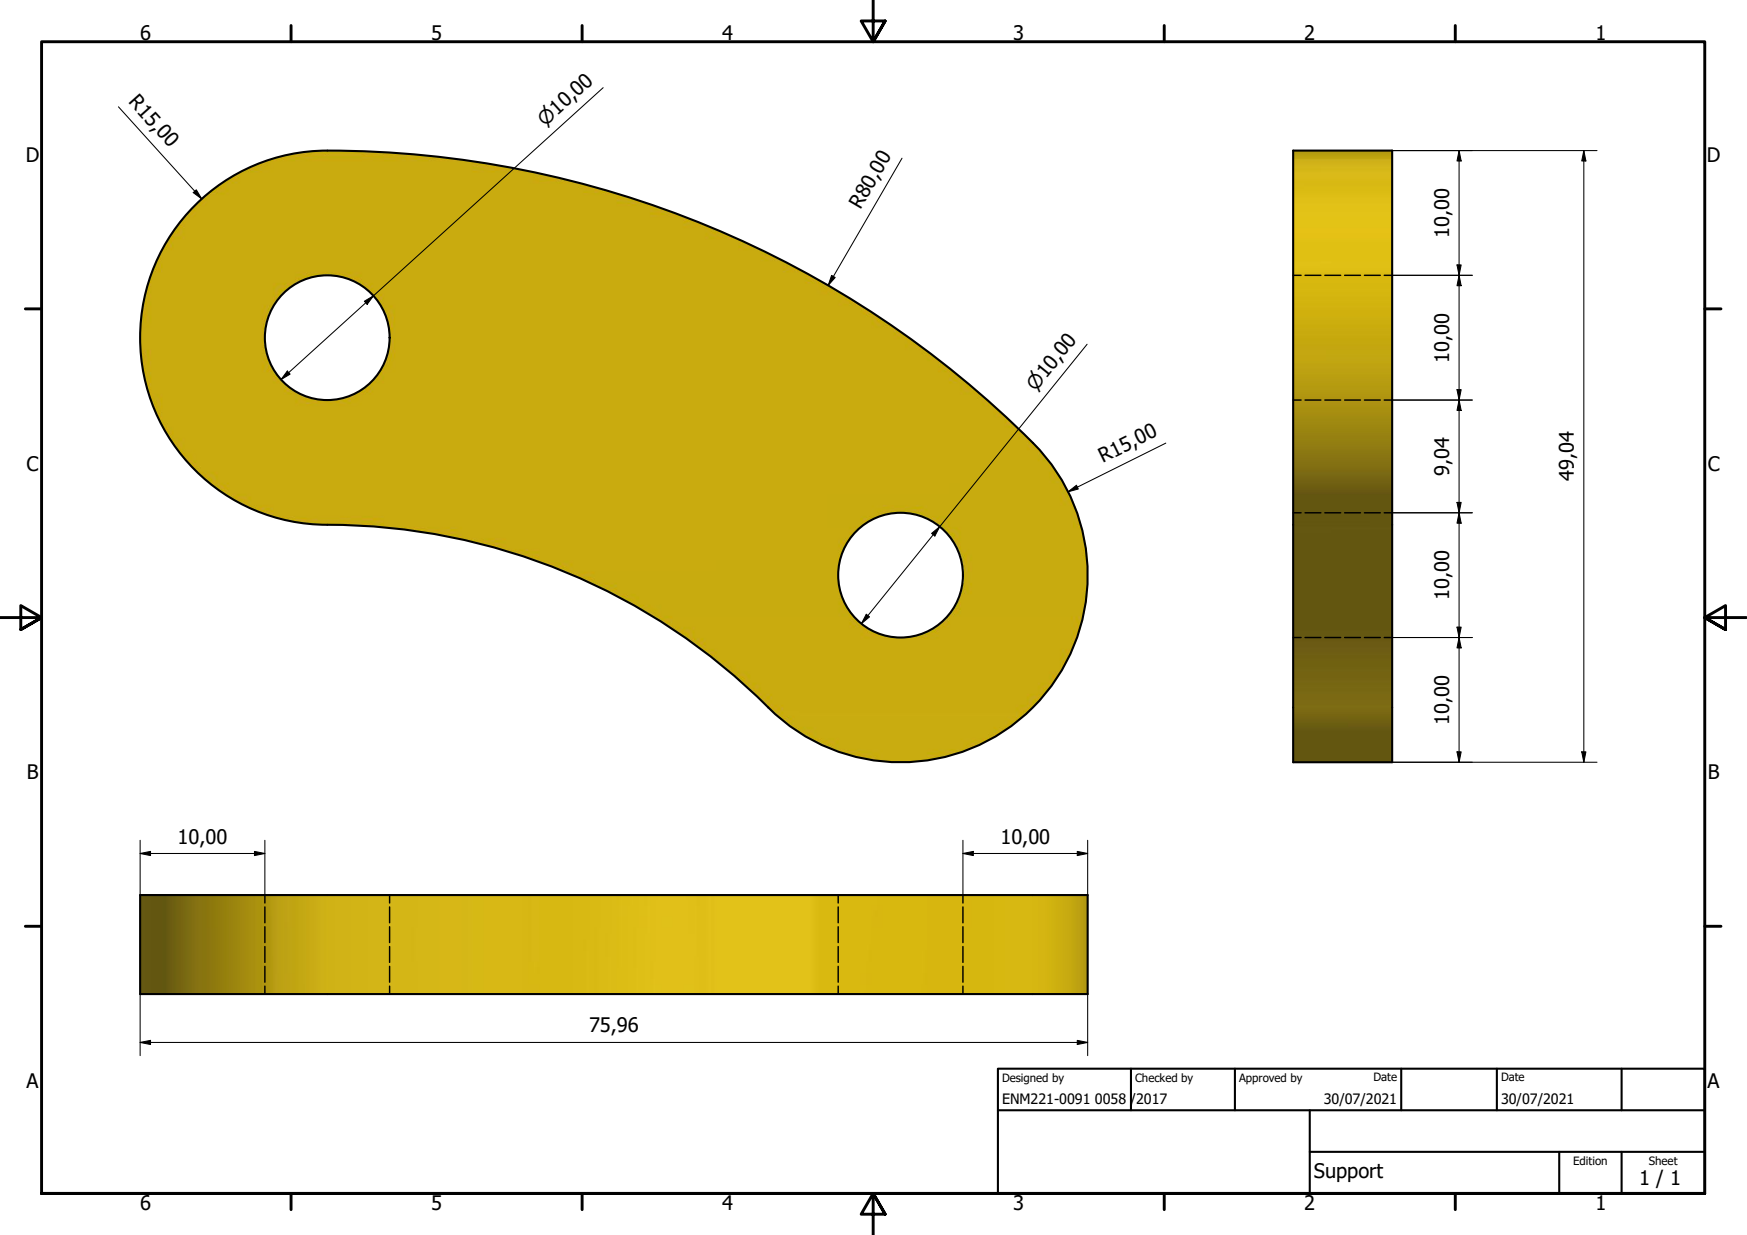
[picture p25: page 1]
ENM221-0091 0058; Designed by; Checked by; Approved by; Date

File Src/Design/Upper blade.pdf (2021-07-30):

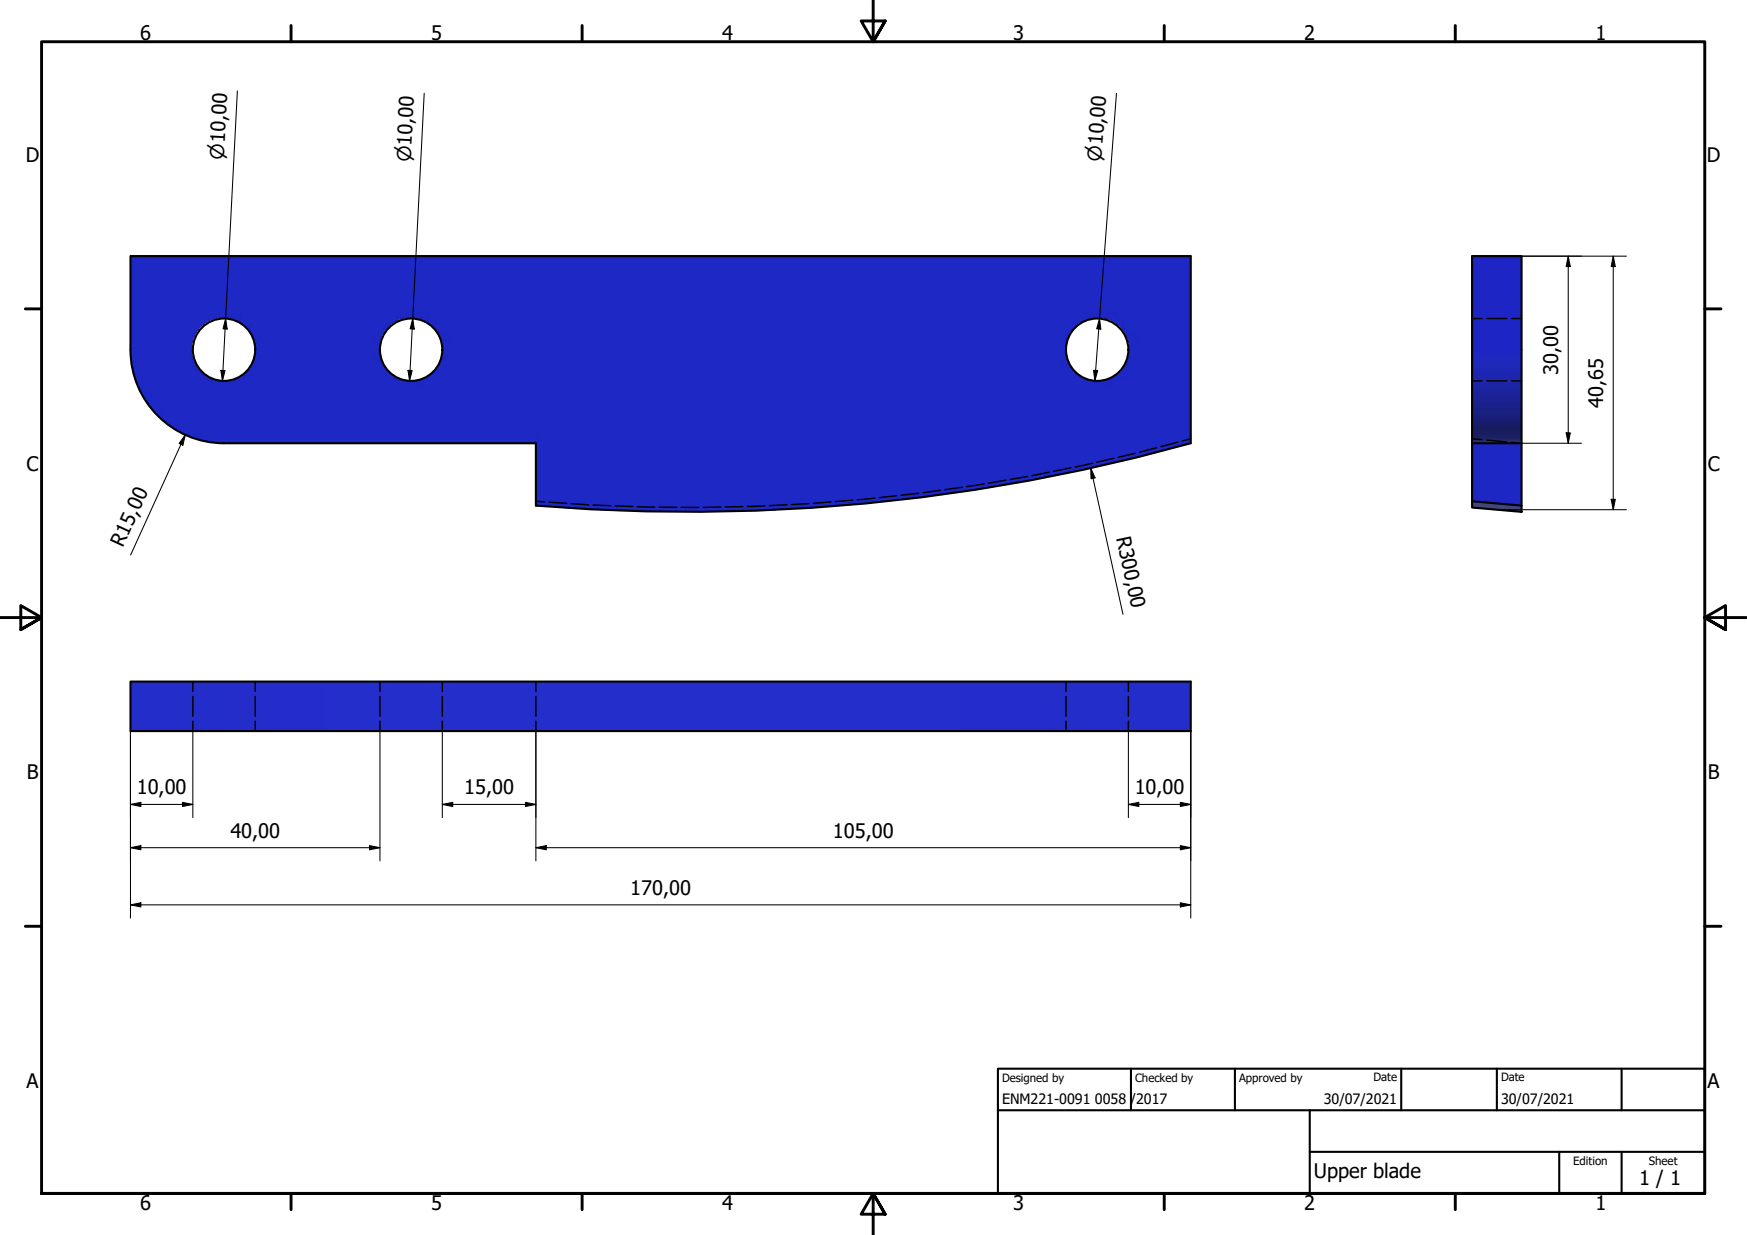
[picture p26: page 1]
Upper blade; ENM221-0091 0058; Designed by; Checked by; Approved by; Date

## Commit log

2021-06-21 Seperate body
    [bodyAssembly.0002.iam, bodyAssembly.iam, bodybottompart.0001.ipt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]
2021-06-24 Proposal changes
    [Lower blade.0001.ipt, Lower blade.ipt, Stand.0001.ipt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]
2021-07-30 Redesign of folder
    [Bolt.ipt, Lower blade.0001.ipt, Lower blade.ipt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]
2021-07-30 Add dwg
    [Bolt.0002.ipt, Bolt.ipt, Lower blade.0001.dwg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]
2021-07-30 Restructure folder
    [Bolt.ipt, Lower blade.0001.ipt, Lower blade.ipt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]
2021-07-30 Add analysis
    [Bolt.0002.ipt, Bolt.0005.ipt, Bolt.ipt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]
2021-07-30 🚧 PROGRESS: Support codes
2021-07-30 🚧 PROGRESS: Upper blade codes
2021-07-30 🎨 IMPROVE: Change name
    [shearningMachineAssembly.dwg]
2021-07-30 🔥 REMOVE: Old versions
    [Support.0003.ipt, Support.0004.ipt, Support.ipt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]
2021-08-01 Add body codes
    [Lower blade.0003.ipt, Lower blade.0004.ipt, Lower blade.ipt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]
2021-08-02 Add all machinings
    [Lower blade.0004.ipt, Lower blade.0005.ipt, Lower blade.ipt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]
2021-08-03 🚧 PROGRESS: Restructure
    [Weld Bead Report.xls, bodytoppart.0007.ipt, bodytoppart.0008.ipt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]
